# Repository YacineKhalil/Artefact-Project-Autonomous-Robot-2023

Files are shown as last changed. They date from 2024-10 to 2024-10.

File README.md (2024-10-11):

# Projet Artefact

### Description du projet

L'idée générale du projet est de faire une voiture téléguidée via une interface web, puis intelligente.

Pour plus de renseignements : [Forum de description du projet](https://discourse.r2.enst.fr/)

### Fiche de présentation du robot

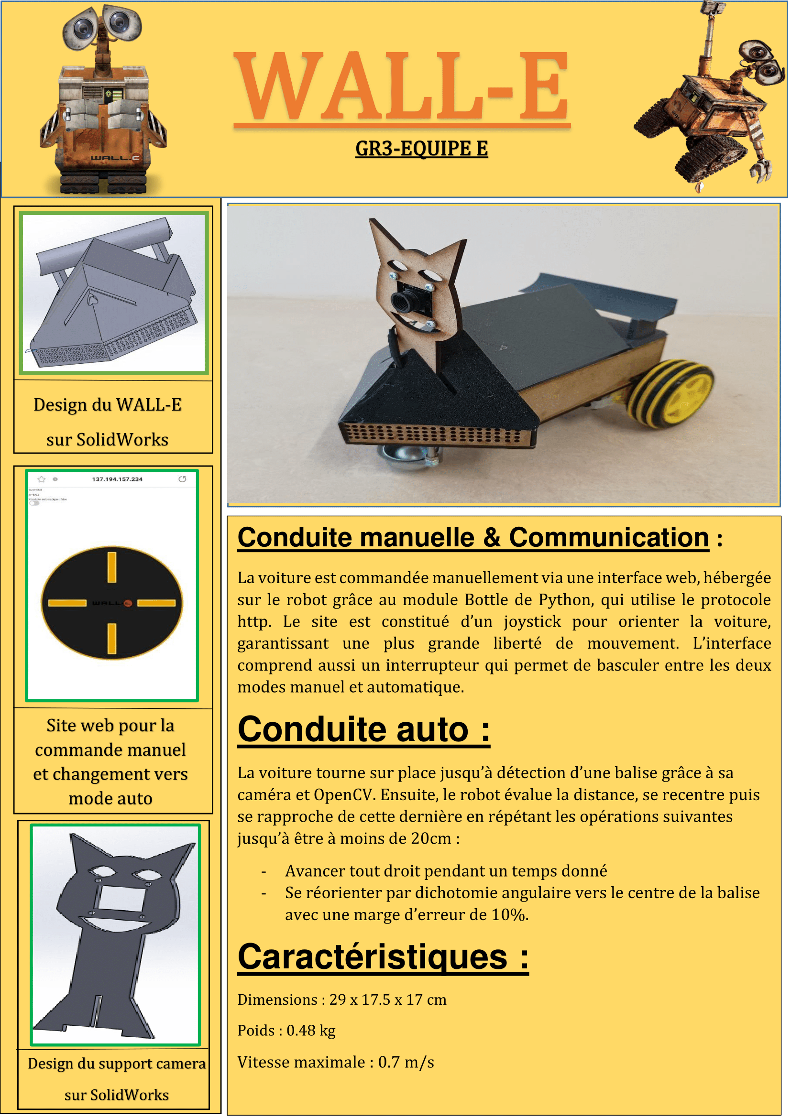
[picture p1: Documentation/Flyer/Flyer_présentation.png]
Flyer


### Explication de notre travail

Pour comprendre notre travail, rendez-vous sur la page [Wiki](https://gitlab.telecom-paris.fr/proj103/2324/gr3/teame/-/wikis/pages) de notre dépôt git, ou suivez l'arborescence des fichiers du dépôt, où sont présents des éléments de documentation.

### Chronologie  du projet

***20/09/2023 :***
-	Connexion en headless depuis le terminal (grâce au rooter)
-	Installation de l’OS pour la raspberry
-	Réflexions sur le design de la voiture 

***27/09/2023 :***
-	Connexion de la carte Raspberry au réseau Campus-Telecom
-	Dépôt git de chaque personne + création d'une clé ssh pour la carte raspberry
-   Connexion de la carte Raspberry au réseau Campus-Telecom
-	Configuration de la date pour la carte Raspberry
-	Documentation pour la caméra 
-	Création du design de la voiture sur SolidWorks

***04/10/2023 :***
-	Optimisation du design et ajout de nouvelles pièces (vis, écrous)
-	Soudure des câbles au moteur
-	Connexion de la caméra sur le Raspberry. 
-	Impression du châssis avec la découpeuse laser. 

***11/10/2023 :*** 
- Installation des paquets pour le moteur et langages de programmation (C, Python)
- Installation de OpenCV et reconnaissance en temps réel de QR Code (avec l'identifiant associé)
- Configuration d'un fichier ".service" qui nous permet de lancer des programmes au démarrage de la Raspberry
- Impression de pièces pour le design de la voiture en 3D 
- Table ronde sur le moyen de contrôler la voiture manuellement : on utilisera une interface web avec un joystick omnidirectionnel

***18/10/2023 :*** 
- Contrôle des moteurs et programmes python pour contrôler la vitesse des moteurs avec la position du joystick
- Installation de Open CV sur la Raspberry
- Développement du site web

***25/10/2023 :***
- Montage de la voiture
- Régression (en 1/x) pour évaluer les distances avec la caméra 
- Détection vidéo des arucos et pilotage automatique en fonction des arucos
- Connexion de la carte Raspberry au site web 
- Contrôle et mise en route de la voiture : session de pilotage depuis l'interface web. 

***14/11/2023 :***
- Modification du sens du Motor Driver (et pour cela soudure de fils) pour éviter de la brûler
- Essais plus poussés de la conduite manuelle de la voiture, vérification que le programme ne s'arrête plus de manière intempestive
- Premiers essais de la conduite automatique

***21/11/2023 :***
- Essais plus poussés de la conduite automatique de la voiture. Nos programmes ne sont pas résilients : la vision n'est pas assez stable.

On recommence le développement en avançant par étape :

-> Création de plusieurs versions du module "capter.py" qui doivent permettre de décider où les capacités de vision limitent la conduite automatique. On avance par palier : 
*1capter.py est plus résilient que 2capter.py, lui-même plus résilient que 3capter.py ...*

-> Le dernier programme capable de capter efficacement un ArUco sera choisi (soit le programme qui minimise le temps d'attente ou de calibrage tout en étant capable de capter et de centrer un ArUco dans son champs de vision avec une forte probabilité).

- Test des fonctions de calcul de l'angle de déviation de la caméra par rapport à un ArUco.

- Nouveau design de support pour caméra afin d'avoir cette dernière à la même altitude que les marqueurs.

***22/11/2023 :***
Travail sur le plan établi le 21/11 :

1) Tester 1capter.py : fonctionne bien
-> on a une fonction résiliente qui cherche un ArUco et s'arrête une fois trouvé

2) Tester 2capter.py : ne fonctionne pas
-> on garde 1capter.py comme architecture de base pour le recherche de marqueurs
Conclusion : on n'arrive pas à capter à coup sûr l'ArUco sans implémenter des périodes où la caméra est fixe.

3) Tester 3recentrer.py : fonctionne bien
-> même principe que 1capter.py en ajoutant à la condition "un aruco est présent dans le cadre" : "le marqueur doit être au centre de l'écran pour l'arrêt du programme"
Conclusion : on a une fonction résiliente qui cherche un ArUco, le cadre dans son champ de vision et s'arrête une fois cette opération effectuée.

4) Combiner 3recentrer avec du mouvement vers l'avant , création d'une boucle :

->Tant que vrai :

    ->si un marqueur est dans le cadre
        ->si le marqueur est centré dans le champ de vision
            ->avance à vitesse vitesse_avance pendant temps_avance secondes
            ->retour début de boucle
        ->sinon
            ->tente de cadrer le marqueur en effectuant une rotation (dans le bon sens) à vitesse vitesse_rotation pendant temps_rotation/3
            ->retour début de boucle

    ->sinon
        ->tente de trouver un marqueur en effectuant une rotation (vers la droite) à vitesse vitesse_rotation pendant temps_rotation
        ->retour début de boucle

5) Recherche du 4-uplet ( vitesse_avance , temps_avance , vitesse_rotation , temps_rotation) qui minimise le temps de parocurs
Conclusion :
-> vitesse_avance et temps_avance ne doivent pas être trop grands sous peine de rentrer dans le marqueur ou de le perdre de vue à chaque fois que la voiture avance.
-> vitesse_rotation et temps_rotation doivent être assez grands pour qu'un tour complet ne prenne pas trop longtemps mais assez petits pour que le recadrage puisse se faire

6) Essais sur les parcours dans l'entrée de l'école
-> Les marqueurs sont moins bien détectés que lors des entraînements précédents
    -> Conclusion rapide que cela est dû à la faible taille du contour blanc autour des balises utilisées par les circuits officiels
    -> Adaptation du code à cette caractéristique

***23/11/2023 :***
Evaluation intermédiaire.
-> Le parcours est réussi dans les temps. La partie manuelle est un succès. Lors de la partie automatique, le véhicule a perdu les 
marqueurs de son champs de vision à deux ou trois reprises mais a tout de même effectué le travail demandé.

Fin résumé des séances à partir de l'évaluation intermédiaire.

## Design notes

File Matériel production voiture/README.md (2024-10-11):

# Production matérielle du robot

Les composants qui nous ont été fournis pour fabriquer notre robot sont les suivants :

    - Ordinateur : Raspberry Pi 5

    - Moteurs : Deux moteurs à courant continu

    - Carte de contrôle des moteurs : Motor Driver HAT for Raspberry Pi, I2C Interface 

    - Roues : Deux roues en plastique

    - Roulette à bille

    - Caméra : Caméra HD 720p USB avec module OV9726

    - Paire de piles et porte-piles

- [Raspberry Pi](https://www.raspberrypi.com/)

- [Roues et moteur](https://www.amazon.fr/Gebildet-DC3V-6V-motrices-robotique-Plastique/dp/B08D39MFN1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)

- [Carte de contrôle des moteurs](https://www.waveshare.com/motor-driver-hat.htm)

### Conception du châssis

La plupart des pièces du robot ont été dessinées sur SolidWorks.

Le format .SDL permet de représenter des desgins de pièces en trois dimensions.

### Utilisation de visserie

Liste de la visserie utilisée :

-	2 vis cruciformes m3/m4 40mm pour roue à bille

-	Ecrous m3/m4 6x : roue à bille + chassis

-	Collier de serrage 4x pour moteur roue arrière 

-	Entretoise x4 M2.5 8mm (Raspberry). 

-	Ecrous M2.5 x4 (Raspberry). 

-	Vis cruciforme TB M2.5 4mm x4. 

Les entretoises permettent de garder une distance entre la carte Raspberry et le châssis de sorte à éviter une surchauffe de l'ordinateur.

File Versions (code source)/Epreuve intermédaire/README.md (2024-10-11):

# Code source pour l'épreuve intermédiaire

Le code source pour l'épreuve intermédiaire se divise en deux parties :

- communication entre le pilote et la voiture (via interface web de joystick)

- pilotage de la voiture (se produit en interne sur la Raspberry)

Ces deux divisions des opérations effectuées par le robot s'exécutent en parallèle (il y a un thread communication parallèlement à un thread pilotage).

Le lien entre ces deux fils d'exécutions est le fichier texte x_y_R_isAuto.txt :

-> La partie communication consiste à modifier le fichier x_y_R_isAuto.txt grâce aux directives du pilote (qui utilise une interface web)

-> La partie pilotage consiste à utiliser les valeurs inscrites dans le fichier x_y_R_isAuto.txt pour contrôler les moteurs

**Pour démarrer le robot dans la logique de l'épreuve intermédiaire, on peut ouvrir deux fenêtres de l'invité de commandes d'un ordinateur, se connecter en ssh au robot sur chacune d'entre elles puis naviguer vers /Communication et vers /Pilotage respectivement. Il reste alors à rentrer les commandes, respectivement :**

> python3 heberger_serveur.py

> python3 main_epreuve_intermediaire.py

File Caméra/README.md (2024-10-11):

# Caméra

### Notre caméra

Caméra HD 720p USB avec module OV9726

### Marqueurs ArUco

Les marqueurs ArUco sont des marqueurs semblables aux QR Code. Il existe différentes bibliothèques d'ArUco, dans lesquelles chaque ArUco est associé à un identifiant distinct.

Les marqueurs utilisés pour l'évalutation sont des ArUco au standard 6 × 6, imprimés sur du papier blanc (5cm × 5cm).

### Détection des ArUco

**Important** : Le module utilisé pour détecter les marqueurs est OpenCV (version python). Nous avons remarqué que les marqueurs imprimés avec une large bordure blanche sont bien mieux détectés que ceux découpés sans bordure. 
Cela peut peut-être s'expliquer par le fait que l'algorithme est entraîné sur des images où les QR Code/ArUco sont souvent entourés d'une large bordure blanche (penser à un QR Code que l'on scanne habituellement au milieu de l'écran).
La caméra doit être correctement règlée afin de pouvoir détecter les ArUco correctement.

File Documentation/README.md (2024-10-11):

# Documentation

Ce fichier regroupe toutes les images utiles à la documentation du dépôt (voir fichiers README.md)

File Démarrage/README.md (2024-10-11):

# Amélioration de la vitesse de démarrage du robot

Les modules de ce dossier servent à automatiser le démarrage du robot pour la conduite manuelle (plus généralement dans le cadre de l'épreuve intermédiaire).
Ils permettent ainsi de lancer le robot sans utiliser la connexion en ssh, il faut uniquement connaître l'adresse du robot pour se connecter à l'interface web de contrôle du véhicule.

## Description

On utilise des fichiers .sh (fichier bash de commandes Linux) pour automatiser la procédure.

**->** demarrage.sh exécute tous les scripts python nécessaires au fonctionnement du robot.

**->** parametrage_droit.sh permet de donner tous les droits d'exécution aux scripts précédents (opération à refaire à chaque pull du git)

**->** init_commandes.py réinitialise le fichier de contrôle de la voiture en mode manuel (qui contient avant cette opération les dernières commandes données lors de la précédente utilisation du robot)

Ces fichiers se lancent après allumage de la carte Raspberry, dès lors que cette dernière a accès à une connexion wifi. Cela est permis par manipulation du fichier run-at-startup.service (voir ci-dessous)

## Procédure détaillée à suivre

1] donner le droit d'exécution de script.py à robot-pi12
ligne de commande à entrer après avoir ajouté script.py à la mémoire de la Raspberry :
chmod +x <chemin vers script.py>

ou

faire directement "parametrage_droits.sh" dans la console (ce qui automatise cet octroi de droits pour ne pas avoir à le faire à la main à chaque pull du git)

2] faire exécuter script.py au démarrage de la Raspberry après que le réseau soit disponible
1ère commande qui crée le fichier de configuration :
sudo nano /etc/systemd/system/run-at-startup.service

y copier le texte suivant :
[Unit]
Description=Lance le contrôle de la voiture
Wants=network-online.target
After=network-online.target

[Service]
ExecStart=<chemin vers script.sh (bash)>
Restart=on-failure

[Install]
WantedBy=multi-user.target

3] créer fichier bash pour exécuter un script python
première ligne : #!/bin/bash
deuxième ligne : sudo python3 <chemin_accès/fichier.py>

4] activer les changements (de run-at-startup.service)
1ère commande
systemctl daemon-reload
2ème commande
systemctl enable run-at-startup.service

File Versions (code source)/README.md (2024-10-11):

# Code source

Le code source du robot est écrit exclusivement à l'aide de Python. Le code source se divise en trois partie :

- Une bibliothèque de fonctions utiles à la fois pour la conduite manuelle et pour la conduite automatique (et donc pour l'épreuve intermédiaire et pour l'épreuve finale)

- Le code source pour l'épreuve intermédiaire

- Le code source pour l'épreuve finale, qui réutilise la logique du code précédent, avec ajout de communication par websockets et d'opérations asynchrones (dans le cadre de la communication avec les autres robots)

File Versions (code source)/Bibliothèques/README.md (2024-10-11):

# Bibliothèque de fonctions python

Tous les scripts utiles au fonctionnement de la voiture en mode manuel ou automatique sont regroupés ici.

## B_conduite_auto.py

Ensemble des fonctions liées à la vision, utiles pour le mode conduite automatique : estimation de la distance à un ArUco, estimation de l'angle d'inclinaison par rapport à la normale à un ArUco ...

Explications :

## Distance à un marqueur :

distance_1

distance_2

distance_3

## Inclinaison à la normale d'un marqueur :

deviation_1

deviation_2

## B_fonctions_calibrage.py

Fonctions utiles pour calibrer les moteurs afin de pouvoir faire avancer le robot d'un nombre de mètres déterminé et afin de pouvoir le faire tourner d'un angle déterminé (nous ne disposons pas d'un retour sur la vitesse de rotation des roues, qui aurait pu permettre de se passer de ce genre de calibrages)

L'idée est globalement de faire une règle de proportionnalité en utilisant time.sleep : 

 > Si en ayant tourné à vitesse v_rotation pendant T secondes on a fait une rotation de alpha degrés, pour faire une rotation de beta degrés on peut tourner à vitesse v_rotation pendant beta * (T/alpha) secondes

## B_lecture_bibli.py

Cette fonction est utile pour le contrôle du robot en mode manuel (voir documentation du dossier Communication dans Epreuve_intermediaire).

## B_module_moteur.py

Le script B_module_moteur.py permet de contrôler les moteurs via le simple appel de la fonction MotorDriver.MotorRun.

Un code similaire est présent sur le site du fabricant du motor driver :

[Documentation de la carte de contrôle des moteurs](https://www.waveshare.com/wiki/Motor_Driver_HAT)

Le script utilise la bibliothèque PCA9685 qui réalise un asservissement des moteurs grâce à la carte de contrôle des moteurs.

## B_module_vitesse.py

Ce fichier est utilisé lors de la conduite en mode manuel, afin de faire le lien entre la position du click du pilote et le contrôle des moteurs (soit la tension à appliquer à chacun des moteurs).

Le pilote dispose d'un joystick et la position de son click est utilisée par le module vitesse selon ces principes :

docu_calcul_U1_U2-1

docu_calcul_U1_U2-2

docu_calcul_U1_U2-3

docu_calcul_U1_U2-4

## B_PCA9685

[Documentation de la carte de contrôle des moteurs](https://www.waveshare.com/wiki/Motor_Driver_HAT)

Ce module a été entièrement repris du site du fabricant de la carte de contrôle des moteurs, et est utile dans la mise en rotation de chaque moteur.

## B_rencentre_bibli.py

Ce fichier est utilisé par le robot pour centrer un ArUco dans son champ de vision, lors de la conduite automatique.

Détail en pseudo-code de la méthode pour ce faire :

    ->Tant qu'on n'a pas centré dans le champ de vision un ArUco de la parité désirée

    ->s'immobiliser

    ->prendre plusieurs captures de l'écran

    ->si aucun ArUco n'est détecté

        ->si un ArUco a déjà été vu mais qu'il n'a pas été centré (on l'a perdu de vue pendant le recadrage)

            ->pivoter à gauche sur place

        ->sinon

            ->pivoter à droite sur place

    ->sinon (un ArUco est détecté)

        -> tourner à droite jusqu'à ce que l'ArUco soit centré dans le champ de vision (<=> la moyenne des abscisses des coins du marqueur est à peu près nulle)

## B_recentrer_mvmt_bibli.py

Le script B_recentrer_mvmt_bibli.py associe les fonctionnalités du fichier précédent à un mouvement rectiligne.

## B_stop_motor.py

Ce module permet d'arrêter le fonctionnement des deux moteurs présents sur la voiture, et est notamment utile lorsque le contrôle du robot a été perdu, afin d'éviter une collision.

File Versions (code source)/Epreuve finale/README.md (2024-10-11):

# Code source pour l'épreuve finale

L'épreuve finale consiste en un parcours complexe et simultané de cinq robots. Chaque robot se repère grâce à des ArUco.

[Modalités de l'épreuve finale](https://discourse.r2.enst.fr/t/seance-evaluation-finale/381/3)

## Fonctions de la bibiliothèque

Tous les fichiers commençant par 'B_" font partie d'une bibliothèque commune aux épreuves finale et intermédiaire. Leur fonctionnement est détaillé dans le dossier Bibliothèques.

## Fonctions de notre groupe

Les fichiers fonctions_communes.py et protocol.py ont été développés par le groupe entier et permettent de mettre en oeuvre notre stratégie et la communication entre robots par laquelle elle passe. Des éléments de documentation sont présents sur le dépôt commun :

[Dépôt de groupe](https://gitlab.telecom-paris.fr/proj103/2324/gr3/depot-groupe)

## main_epreuve_finale.py

**Le script main_epreuve_finale.py est lancé en ssh lorsque le robot qui agit comme serveur a lancé ce dernier.**

On utilise la bibliothèque asyncio afin de réaliser des opérations asynchrones (attente d'informations de la part du robot serveur).

On réutilise aussi les fonctions développées pour l'épreuve intermédiaire (voir le fichier associé)

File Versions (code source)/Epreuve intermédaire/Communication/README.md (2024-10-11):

# Communication entre le pilote et le robot par interface web

La communication se fait via wifi, en utilisant un navigateur internet quelconque sur un ordinateur/téléphone connecté au même réseau wifi que la Raspberry du robot. Pour se connecter à l'interface web, il faut entrer dans la barre de recherche du navigateur :

> (adresse ip du robot):8080/static/site_joystick

Il est possible de connaître l'adresse ip du robot depuis un invité de commandes en appelant :

> hostname -I

## Serveur

Le serveur est hébergé directement sur la Raspberry, en excécutant la commande :

> python3 heberger_serveur.py

Ce serveur tourne grâce au module Bottle de python, solution légère qui se base sur le protocole http (Bottle est similaire à Flask).

Lorsque le pilote se connecte au serveur ouvert, ce dernier lui envoie les fichiers de static, puis l'appareil du client renvoie toutes les 0.1 secondes les données de son click, grâce à la méthode POST. Alors ces données sont inscrites dans le fichier x_y_R_isAuto.txt grâce à la fonction de stocke_donnees.py.

## Interface web

L'interface web fonctionne grâce aux fichiers du dossier static (image d'un joystick, fichier css pour la présentation visuelle du site web, fichier html pour la structure de base du site et fichier js pour l'interactivité de l'interface), servies par le serveur. 

Le fichier js permet notamment de déterminer le lieu du click du pilote par rapport au centre du joystick.

Un interrupteur permet de passer du mode conduite manuelle au mode conduite automatique et inversement.

Visuel de l'interface :

interface_web

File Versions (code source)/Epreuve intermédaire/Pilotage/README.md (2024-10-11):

# Exécution locale sur la Raspberry

Le dossier Pilotage est dédié à des fonctions qui s'exécutent localement sur la Raspberry (à l'inverse dossier Communication). Elles permettent entre autres de contrôler les moteurs.

## Fonctions de la bibiliothèque

Tous les fichiers commençant par 'B_" font partie d'une bibliothèque commune aux épreuves finale et intermédiaire. Leur fonctionnement est détaillé dans le dossier Bibliothèques.

## Bruit moteur

Le bruit de moteur est une fonctionnalité qui a été ajoutée à la fin du projet pour le loisir. L'intensité du bruit s'adapte en fonction de la vitesse de la voiture.

## main_intermediaire.py

Le fichier main_intermediaire.py doit être lancé lorsque le serveur est hébergé.

    Le script récupère d'abord les valeurs inscrites dans x_y_R_isAuto.txt (dossier Communication)

    Si le bouton de conduite automatique est désactivée

        Le script rentre dans le mode conduite manuelle, avec les paramètres récupérés dans x_y_R_isAuto.txt

    Sinon

        Le script rentre en mode conduite automatique

            Faire en boucle les opérations 

            La voiture cherche un marqueur (pair ou impair en fonction des instructions de l'épreuve intermédiaire)

            Elle cadre le marqueur trouvé dans son champ de vision

            Elle avance sur une durée déterminée

            Elle s'arrête

            Revenir en début de boucle

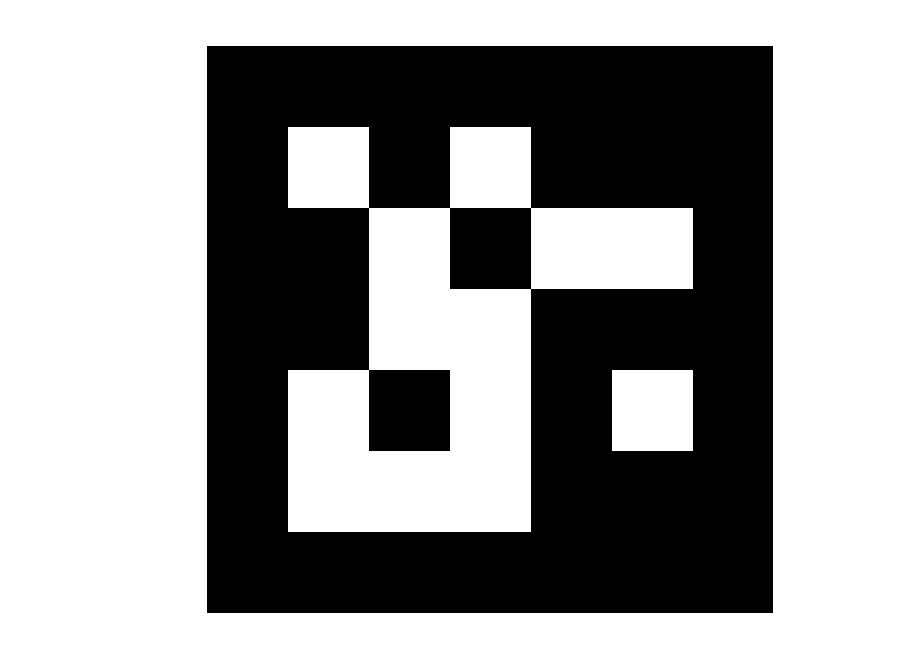
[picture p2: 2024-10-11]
Caméra/Exemples de marqueurs ArUco/aruco1.png

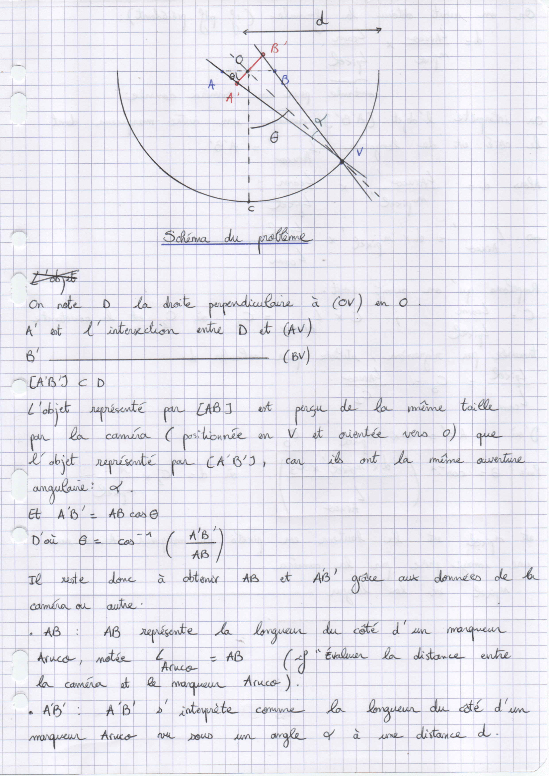
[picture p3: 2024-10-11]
Documentation/Vision/deviation_1.png

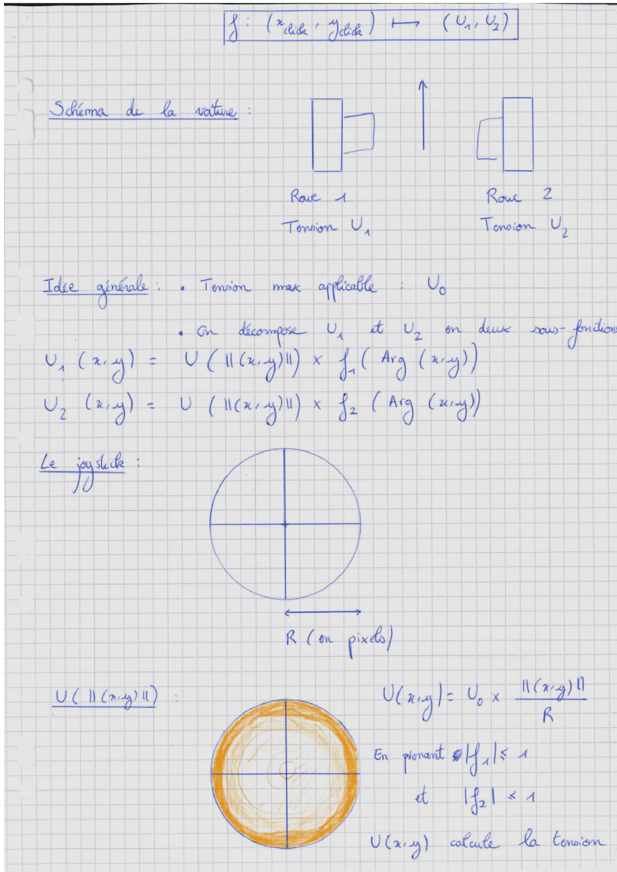
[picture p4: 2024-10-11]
Documentation/Conduite/docu_calcul_U1_U2-1.png

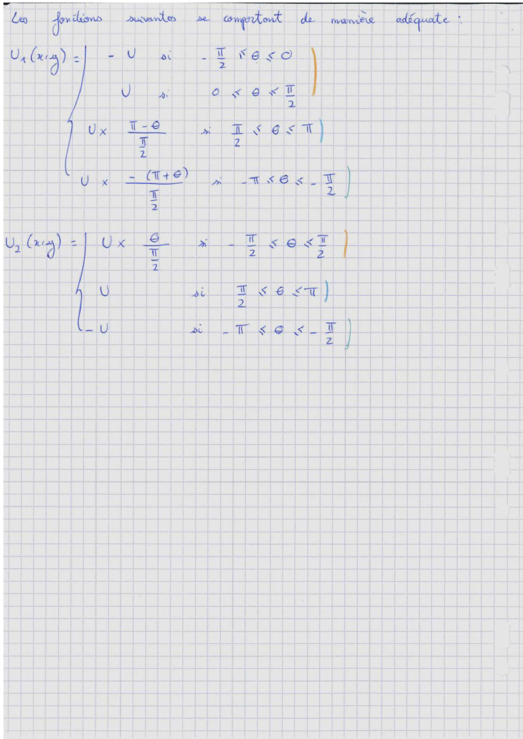
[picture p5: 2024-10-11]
Documentation/Conduite/docu_calcul_U1_U2-4.png

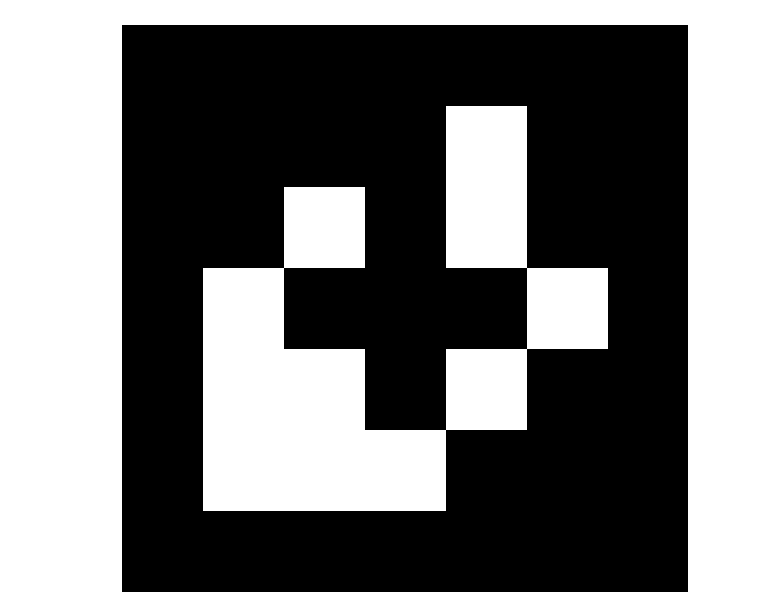
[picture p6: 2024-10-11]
Caméra/Exemples de marqueurs ArUco/aruco2.png

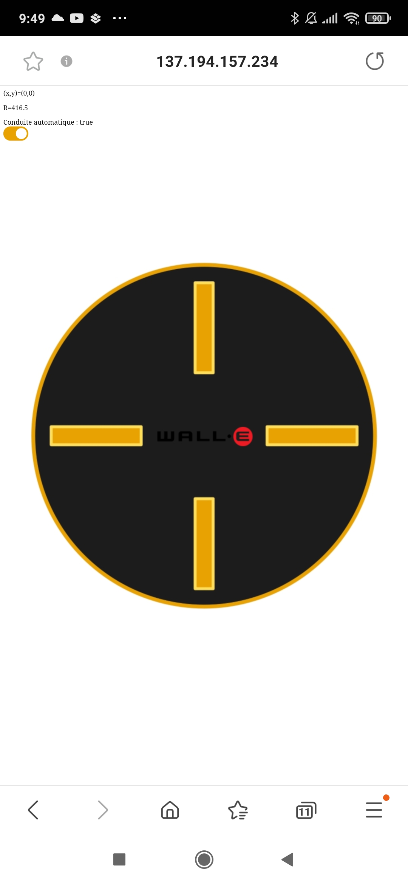
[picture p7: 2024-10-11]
Documentation/Interface/interface_web.jpg

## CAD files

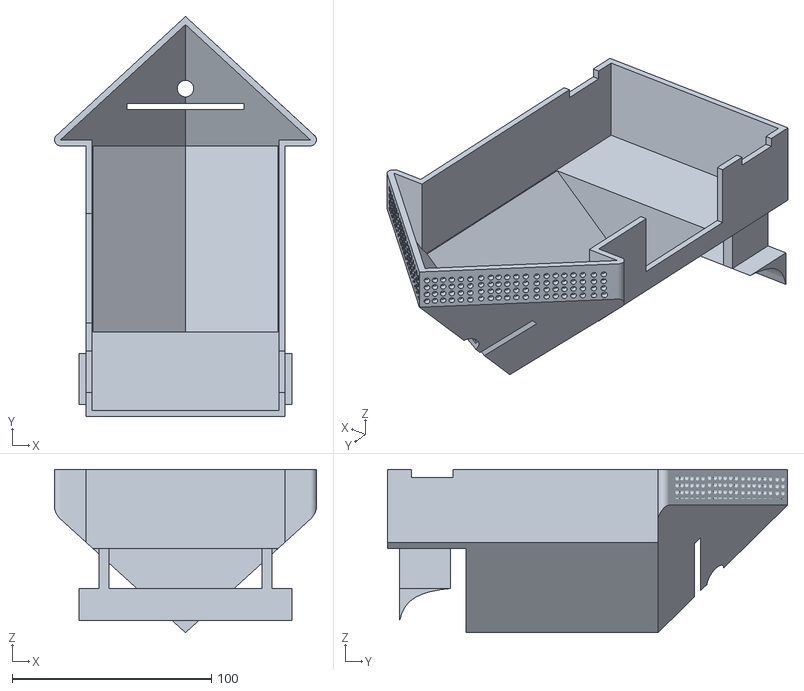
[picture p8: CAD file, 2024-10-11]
Matériel production voiture/Carcasse et caméra/model 2 .STL
131.6 x 201.0 x 82.1

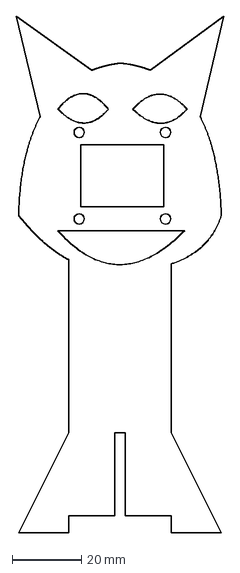
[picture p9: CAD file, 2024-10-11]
Matériel production voiture/Plans des pièces/camera1.DXF
60.0 x 149.6 mm

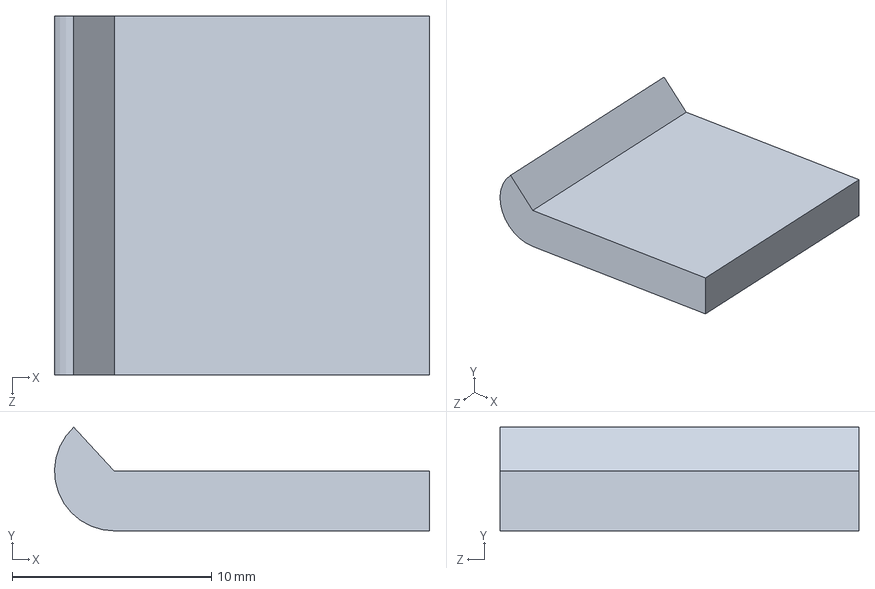
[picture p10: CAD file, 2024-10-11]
Matériel production voiture/Plans des pièces/machine 3d/7.SLDPRT
18.8 x 5.21 x 18.0 mm

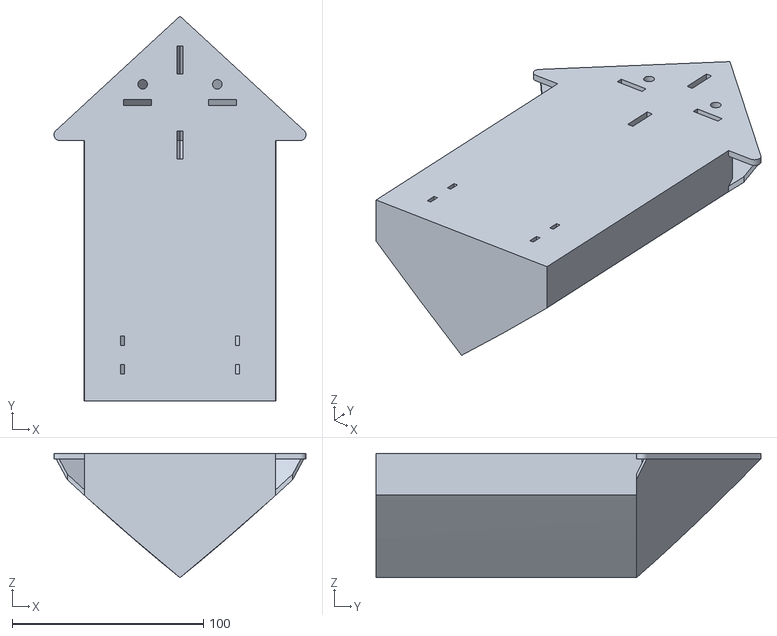
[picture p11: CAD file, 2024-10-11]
Matériel production voiture/Carcasse et caméra/model 1 .STL
131.6 x 201.0 x 65.0

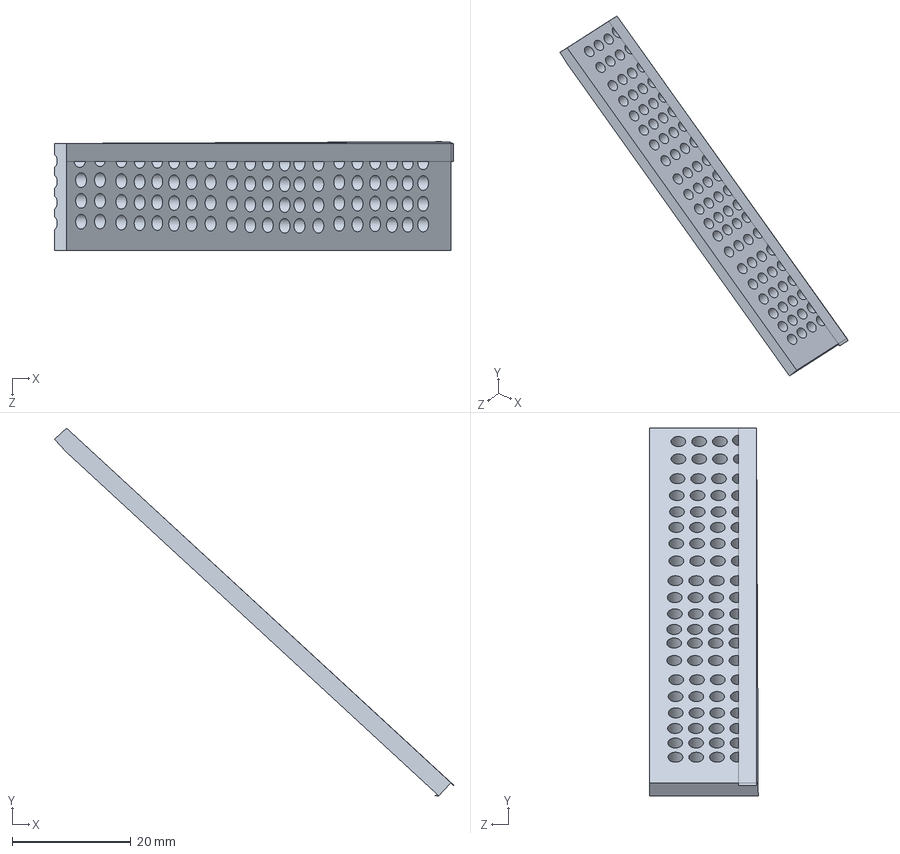
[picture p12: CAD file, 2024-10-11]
Matériel production voiture/Plans des pièces/5.SLDPRT
67.3 x 62.0 x 18.3 mm

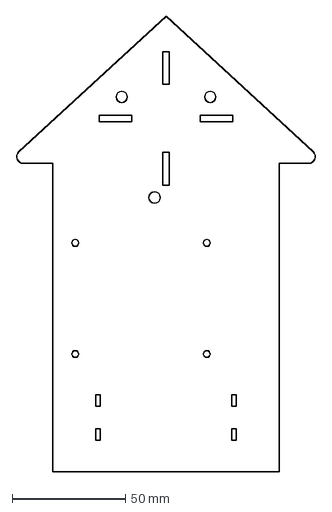
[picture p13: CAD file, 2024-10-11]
Matériel production voiture/Carcasse et caméra/Châssis_prototype_1.DXF
132.1 x 201.0 mm

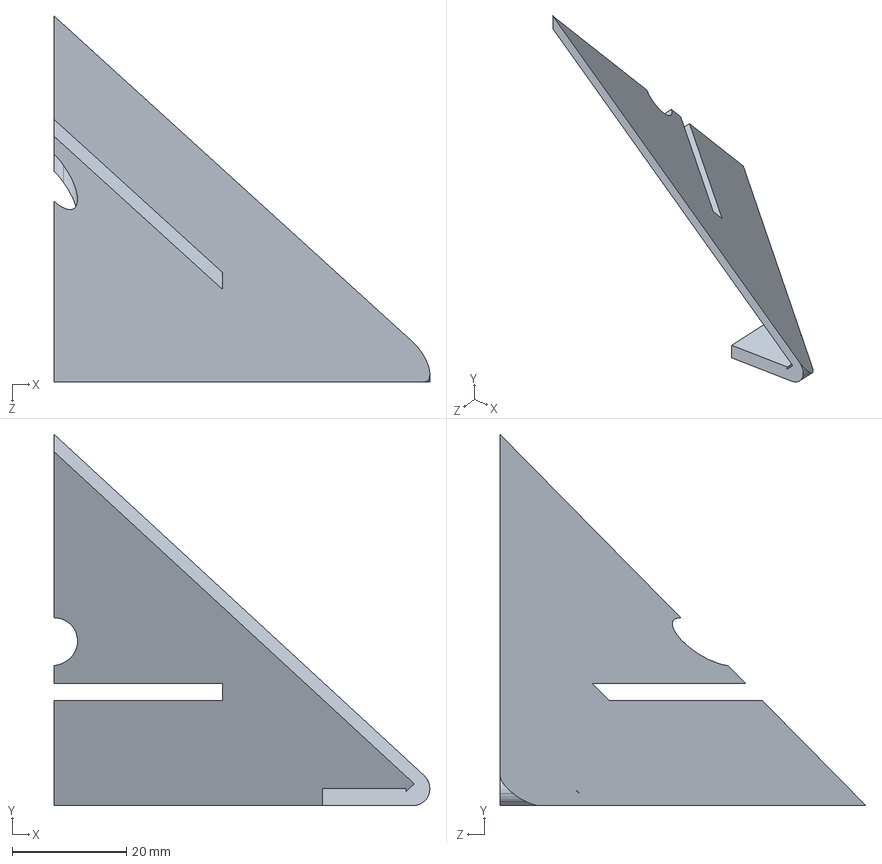
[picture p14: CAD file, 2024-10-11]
Matériel production voiture/Plans des pièces/machine 3d/4.SLDPRT
65.8 x 65.0 x 64.1 mm

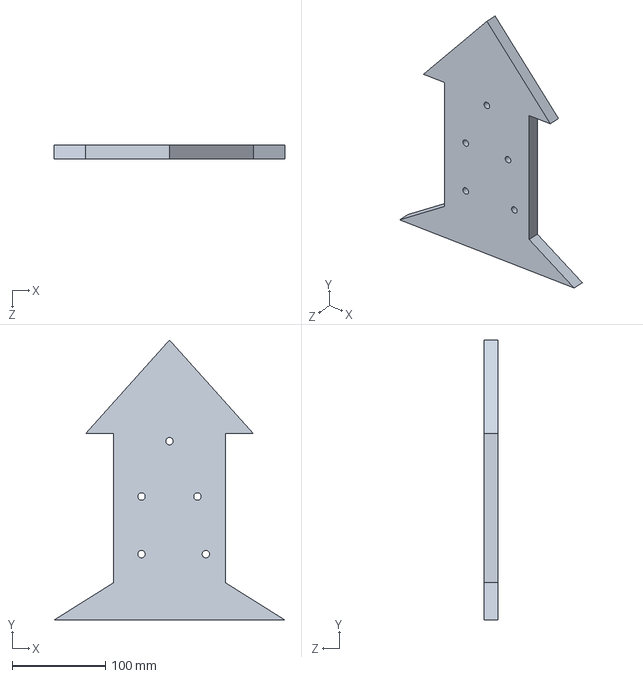
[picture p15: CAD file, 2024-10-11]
Matériel production voiture/Plans des pièces/Pièce1.SLDPRT
247.6 x 300.4 x 15.0 mm

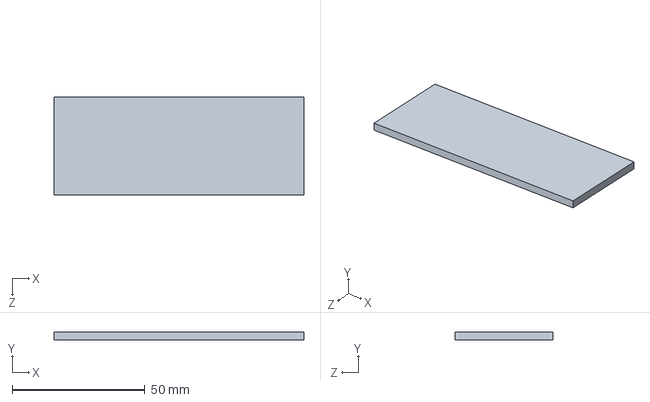
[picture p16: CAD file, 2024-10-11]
Matériel production voiture/Plans des pièces/3.SLDPRT
94.0 x 3.00 x 36.9 mm

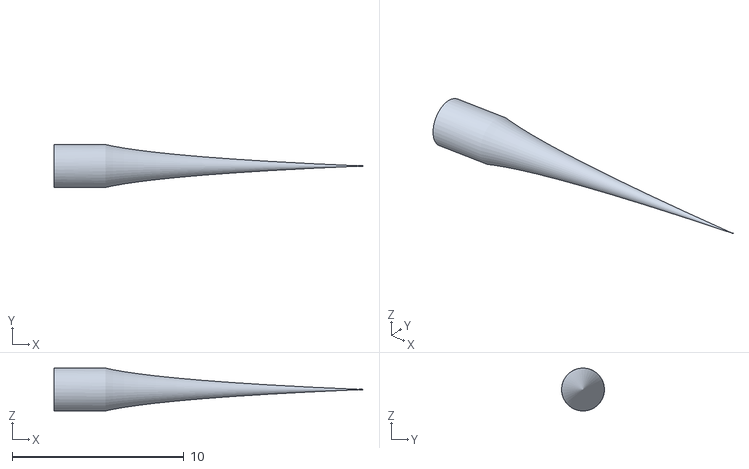
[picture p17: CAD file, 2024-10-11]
Matériel production voiture/Plans des pièces/machine 3d/pick.STL
18.0 x 2.50 x 2.50

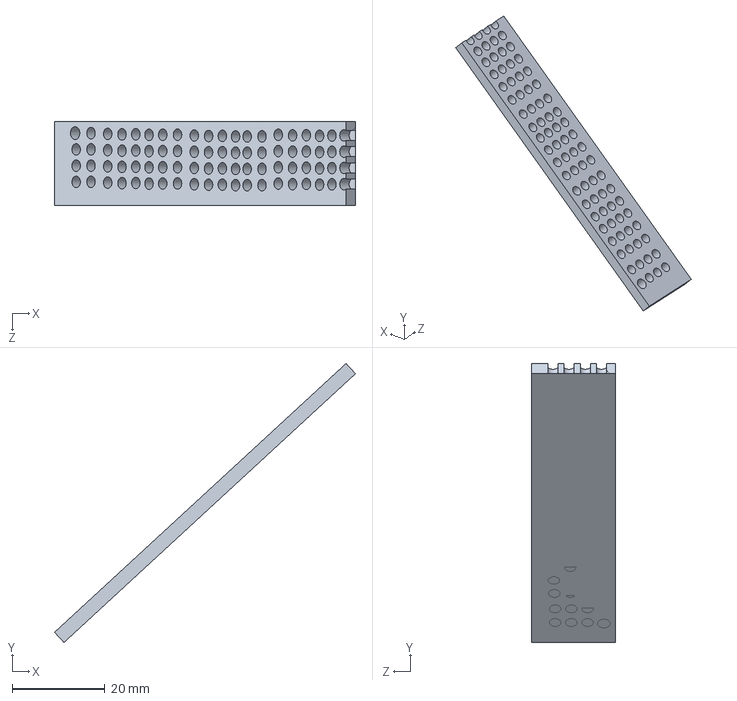
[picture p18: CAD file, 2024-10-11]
Matériel production voiture/Plans des pièces/6.SLDPRT
64.9 x 60.1 x 18.0 mm

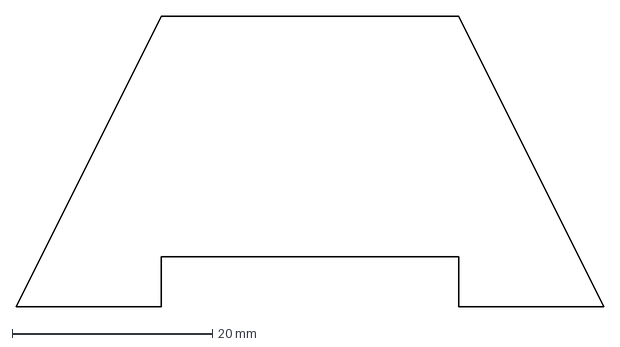
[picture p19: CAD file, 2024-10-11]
Matériel production voiture/Plans des pièces/camera.DXF
58.7 x 29.0 mm

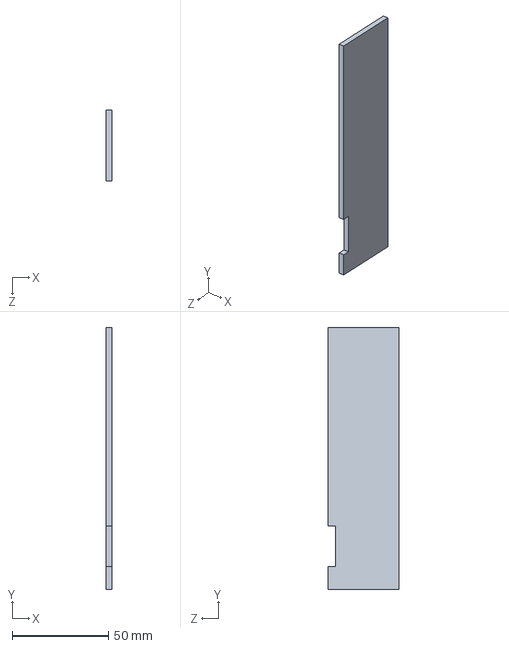
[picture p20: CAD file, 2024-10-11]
Matériel production voiture/Plans des pièces/2.SLDPRT
3.00 x 136.0 x 36.9 mm

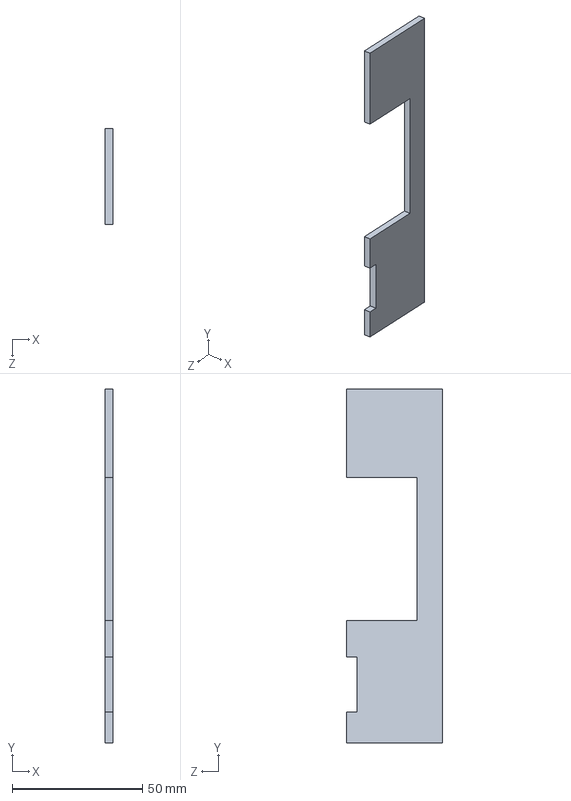
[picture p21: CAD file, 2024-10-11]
Matériel production voiture/Plans des pièces/1.SLDPRT
3.00 x 136.0 x 36.9 mm

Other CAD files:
Matériel production voiture/Plans des pièces/machine 3d/8.SLDPRT
Matériel production voiture/Plans des pièces/1.DXF
Matériel production voiture/Plans des pièces/2.DXF
Matériel production voiture/Plans des pièces/3.DXF
Matériel production voiture/Plans des pièces/5.DXF
Matériel production voiture/Plans des pièces/6.DXF
Matériel production voiture/Plans des pièces/machine 3d/4.STL
Matériel production voiture/Plans des pièces/machine 3d/7.STL
Matériel production voiture/Plans des pièces/machine 3d/8.STL

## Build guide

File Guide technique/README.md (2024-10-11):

# Guide développeur

Ce guide recense les méthodes importantes que nous avons suivies pour développer le robot.

**NB** : Avant que la Raspberry ait accès au wifi, les manipulations peuvent être faites directement sur la carte usb insérée dans la Raspberry (en la mettant dans un autre ordinateur)

# Configuration wifi

### La première étape pour pouvoir communiquer avec la Raspberry Pi via wifi est de connecter la carte à un réseau

Lorsque le réseau wifi nécessite un certificat, il faut mettre le fichier de certificat dans le boot et effectuer d'autres opérations : [suivre ce lien](https://discourse.r2.enst.fr/t/configuration-wpa-supplicant-pour-le-reseau-campustelecom/269)

# Connexion ssh

### Pour pouvoir communiquer avec la Raspberry Pi via wifi et ainsi modifier son code source, on peut utiliser l'invité de commandes de n'importe quel ordinateur

Pour ce faire, il faut ajouter une des clefs ssh de l'ordinateur depuis lequel on veut contrôler la Raspberry dans un dossier spécifique : [lien vers un tutoriel](https://www.raspberryme.com/configuration-des-cles-ssh-sur-le-raspberry-pi/)

Moralement, on donne ainsi le contrôle de la Raspberry aux ordinateurs associés aux clefs ssh ajoutées.

Il est alors possible de se connecter en ssh à la Raspberry depuis un ordinateur autorisé et connecté au même wifi en ouvrant un invité

**Commande pour se connecter à la raspberry (sur campus telecom) :**

> ssh pi@robotpi-12.enst.fr

**Commande pour éteindre le raspberry :**

> sudo poweroff 

**Si la raspberry est connectée sur un rooter plutôt que sur le wifi Campus-Télécom, on fera plutôt :**

> ssh pi@robotpi-12.enst.fr

# Utiliser GIT pour développer facilement une solution

### Configuration du GIT sur l'ordinateur de chaque développeur

- Installer git au préalable.

- Générer une clé SSH via ssh-keygen

- Mettre la clef dans une destination, la clé ssh sera notée .ssh dans les dossiers. 
Il peut être judicieux d'ajouter un mot de passe à cette clef.

Il est important de bien différencier deux fichiers dans le cadre du chiffrement asymétrique :

Clé privée **->** id_rsa 
Cette clé ne doit en aucun cas être partagée

Clé publique **->** Id_rsa.pub 
Cette clé a vocation à être partagée

Ensuite, il convient d'ajouter sa clé sur le gitlab

### Liste de quelques commandes utiles

Pour récupérer les dossiers : 

> git clone <lien_projet> ; 

cette commande est à faire dans le fichier où je souhaite créer une copie du dépôt

Faire un dépôt :

> git add <name_file> 

(pour un seul fichier)

> git add -A 

(pour tous les fichiers). 

Pour le commit (avant envoi) : 

> git commit -m  "résumé des modifications apportées"

Pour envoyer :

> git push

Remarque : S’il y a eu une modification entre temps : 

>git pull. 

Informations pour le dépôt git de notre raspberry : 

MDP : walle

Full Name : Walle-E

Room number : 12

# Mettre la Raspberry à l'heure

Pour mettre à l'heure la Raspberry (connectée au wifi), il est possible de suivre les étapes suivantes :

Accéder au dossier de configuration : /etc/systemd/timesyncd.conf

Utiliser la commande cd nano (dans l'invité) pour modifier le fichier :

    [Time]

    NTP=ntp.enst.fr

    FallbackNTP=0.debian.pool.ntp.org 1.debian.pool.ntp.org 2.debian.pool.ntp.org 3.debian.pool.ntp.org

Puis utiliser la suite de commandes dans l'invité :
> sudo systemctl enable systemd-timesyncd.service

> sudo systemctl start systemd-timesyncd.service

> sudo systemctl restart systemd-timesyncd.service

On pourra ensuite utiliser la commande dans l'invité

> date

pour afficher la date.

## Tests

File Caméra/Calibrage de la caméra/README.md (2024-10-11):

### Estimation de la distance à un marqueur

Le bon calibrage de la caméra permet d'estimer la distance du robot à un ArUco qu'il détecte.

Ce calibrage dépend en fait essentiellement de la distance focale de la caméra et du maillage en pixel du capteur (voir le pdf idoine)

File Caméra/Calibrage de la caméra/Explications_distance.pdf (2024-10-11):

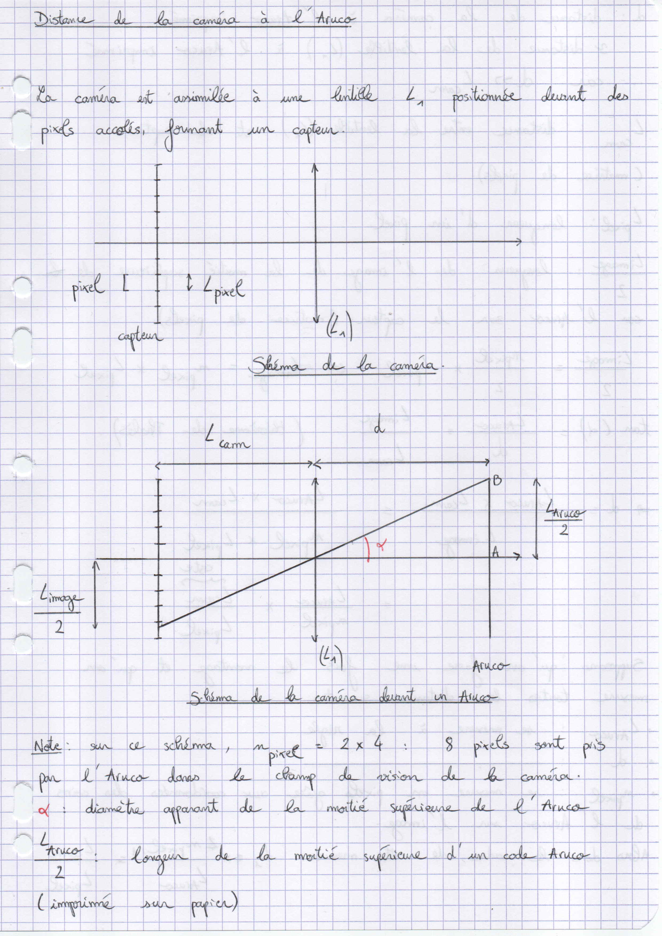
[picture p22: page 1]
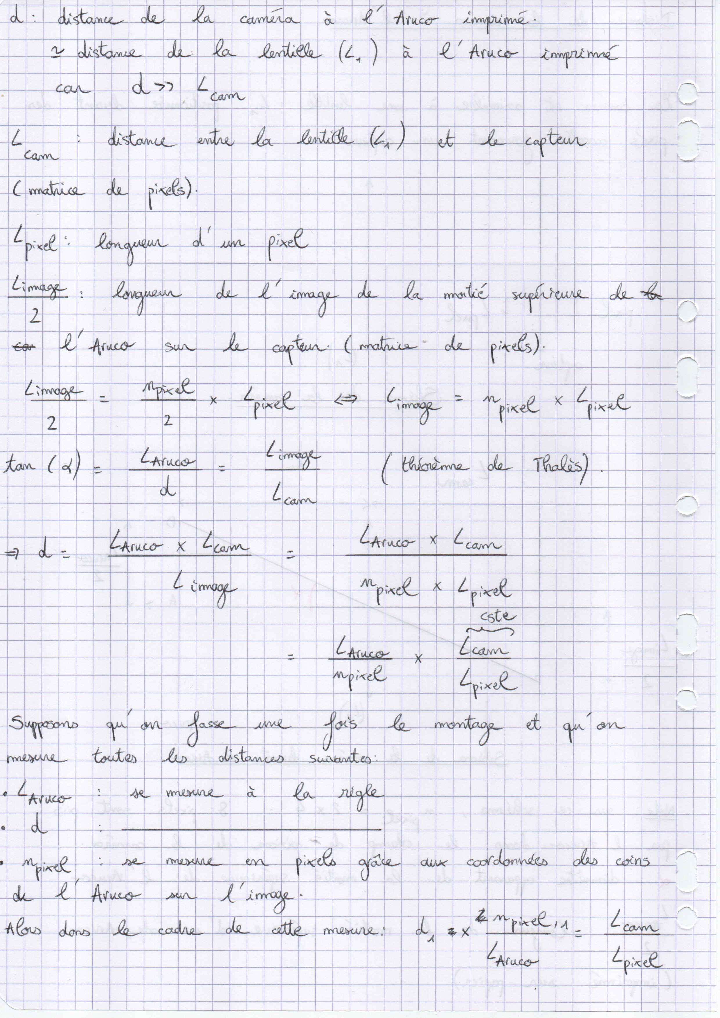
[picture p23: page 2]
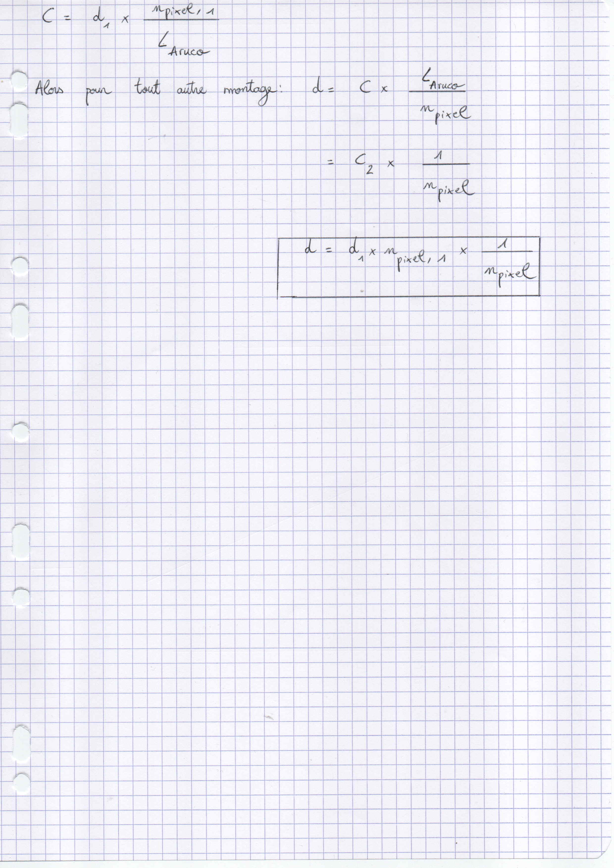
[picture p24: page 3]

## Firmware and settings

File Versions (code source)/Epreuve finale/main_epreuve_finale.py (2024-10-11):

import B_fonctions_calibrage as mvmt
import B_module_moteur as m
import B_conduite_auto as ia
import B_recentrer_mvmt_bibli as R
import B_recentre_bibli as C
import protocol as pr
import fonctions_communes as fc
import cv2
import cv2.aruco as aruco
import websockets
import time
import asyncio


ordre = [3,5,1]
cap = cv2.VideoCapture(0) #on ouvre la vidéo dès le début

#cap.set(cv2.CAP_PROP_FPS,30.0)
#cap.set(cv2.CAP_PROP_FRAME_WIDTH,1280)
#cap.set(cv2.CAP_PROP_FRAME_HEIGHT,720)
#cap.set(cv2.CAP_PROP_FOURCC,cv2.VideoWriter.fourcc('M','J','P','G'))

async def run():
    alpha = 0
    # ETAPES POUR TOUTES LES VOITURES (sauf la première):*
    #   - Ouvrir la connexion
    ws = await pr.open_connection(12)
    balises = await pr.get_ordre_balise(ws)
    position = [balises[str(b)] for b in ordre]
    print('balises',balises)

    #   - Attendre le go
    print("On attend de pouvoir partir")
    while not await pr.can_go(ws,0,0):
        print("on attend de pouvoir partir")
        time.sleep(0.5)

    #   - Aller au milieu
    print("On avance au milieu")
    mvmt.avancer(2.5) #avancer de 2.5m

    #   - Chercher notre balise grace a l'information donnée
    print("On s'oriente vers la première balise")
    mvmt.angle(-45*position[0]) # dans notre convention angle > 0 = sens trigo (tourner gauche)

    #       - Si problème de balise non trouvée chercher normalement
    #   - Aller à la balise
    
    await pr.send_signal(ws,1,ordre[0])
    # avancer de x metre
    print("On part vers la première balise")
    R.avance_vers_aruco(ordre[0],cap) #aller vers balise ordre [0]

    #   - Envoyer un signal quand on est arrivé
    await pr.send_signal(ws,2,ordre[0])

    aurco = C.multi_cap(20,cap,ordre[0])
    #if aruco == ():
    #    alpha = 0
    #else:
    #    corners = [aruco[1],aruco[2],aruco[3],aruco[4]]
    #    alpha = pr.estimation_angle_aruco(corners)

    #   - Calculer l'angle avec un decalage pour arriver en face
    angle = fc.angle_ij(position[0], position[1], 0.3,alpha)    
    # On peut prendre en compte le fait qu'on connait l'angle d'arrivé donc ne pas se placer a 0.3m (y a la fontion sur le git)
    print("On s'oriente vers la deuxième balise")
    mvmt.angle(-angle)

    #   - Attendre le go
    while not await pr.can_go(ws,2,ordre[0]):
        print("On attend de pouvoir partir")
        time.sleep(0.5)
        
    #   - Aller à la balise
    await pr.send_signal(ws,3,ordre[0])
    print("On part vers la deuxième balise")
    mvmt.avancer(0.5) # on avance de 1m
    R.avance_vers_aruco(ordre[1],cap) #aller vers balise ordre [1]

    #   - Envoyer un signal quand on est arrivé
    await pr.send_signal(ws, 4, ordre[1])

    aurco = C.multi_cap(20,cap,ordre[1])
    #if aruco == ():
    #    alpha = 0 
    #else:
    #    corners = [aruco[1],aruco[2],aruco[3],aruco[4]]
    #    alpha = pr.estimation_angle_aruco(corners)

    #   - Calculer l'angle avec un decalage pour arriver en face
    angle = fc.angle_ij(position[1], position[2], 0.3,alpha)
    print("On s'oriente vers la troisième balise")
    mvmt.angle(-angle)

    #   - Attendre le go
    while not await pr.can_go(ws,4,ordre[1]):
        print("On attend de pouvoir partir")
        time.sleep(0.5)

    #   - Aller à la balise
    await pr.send_signal(ws, 5, ordre[1])
    print("On part vers la troisième balise")
    mvmt.avancer(0.5) # on avance de 1m
    R.avance_vers_aruco(ordre[2],cap) #aller vers balise ordre [2]

    #   - Envoyer un signal quand on est arrivé
    await pr.send_signal(ws, 6, ordre[2])

    aurco = C.multi_cap(20,cap,ordre[2])
    #if aruco == ():
    #    alpha = 0
    #else:
    #    corners = [aruco[1],aruco[2],aruco[3],aruco[4]]
    #    alpha = pr.estimation_angle_aruco(corners)

    #   - S'orienter vers l'arrivée
    angle = fc.angle_ij(position[2], -3.5, 0.3,alpha)  # -3.5 c'est la position 9
    print("On s'oriente vers l'arrivé*")
    mvmt.angle(-angle)

    #   - Attendre le go
    while not await pr.can_go(ws,6,ordre[2]):
        print("On attend de pouvoir partir")
        time.sleep(0.5)

    #   - Aller à l'arrivé
    await pr.send_signal(ws, 7, ordre[1])
    print("On part vers l'arrivé")
    R.avance_vers_aruco(9,cap)

    #   - Envoyer un signal quand on est arrivé
    await pr.send_signal(ws, 8, 9)
    print("On est arrivé à la fin.")


    #   - Se décaler pour laisser les autres voitures passer
    mvmt.angle(45)
    mvmt.avancer(1)

    # POUR TOUTES LES VOITURES ENVOYER DES SIGNAUX DE VIES

if __name__ == "__main__":
    asyncio.get_event_loop().run_until_complete(run())

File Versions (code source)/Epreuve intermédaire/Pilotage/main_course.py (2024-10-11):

import cv2
import time
import instructions_conduite_auto as c_auto
import conduite_manuelle as c_manu
import B_lecture_bibli as lect
import pygame 


#PARTIE CONTROLE DE L'ENCEINTE#

# Adresse MAC de l'enceinte : 00:12:3D:00:2D:86

N=10   #on va utliser un filtre glissant pour avoir l'impression que le bruit du moteur ne saccade pas

pygame.init()
pygame.mixer.init()
sound = pygame.mixer.Sound("bruit_moteur.wav")
sound.set_volume(0)
sound.play(-1)
P_moteur_liste=[0]*N    #N valeurs précédentes : on va faire un lisseur
P_sortie_audio=0

################################

T = True

while T:

    etat = lect.read('/home/pi/artefact/teame/Versions/Epreuve_intermédaire/Communication/x_y_R_isAuto.txt')     # syntaxe requise pour etat: float,float,float,bool

    if etat=="bug communication":
        print(etat)


    else:
        P_new=c_manu.conduite_manuelle(etat)    #applique les tensions au moteur et affecte la valeur de puissance fournie aux moteurs à P_new
        P_moteur_liste.append(P_new)
        print(etat)

        P_last=P_moteur_liste.pop(0)
        P_sortie_audio=P_sortie_audio+(P_new-P_last)/N      #équivalent à faire sum(P_moteur_liste)/len(P_moteur_liste) mais économise des calculs
        sound.set_volume(P_sortie_audio + 0.05)      #+0.05 pour ne jamais avoir un moteur totalement silencieux
        time.sleep(0.1)
